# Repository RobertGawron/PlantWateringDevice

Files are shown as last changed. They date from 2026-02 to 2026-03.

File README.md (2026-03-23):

# Plant Watering Device

  

This is a device for watering indoor plants based on the 8-pin PIC10F202-IOT microcontroller.

The goal is to try to make a project on this small MCU and learn how to deal with the limitations of such a small chip, as well as to learn the PIC MCU family ecosystem.

Features:

* **Sensing soil humidity** using a cheap capacitance sensor
* **Display of actual soil humidity and low-level soil humidity when the watering is started;** what is presented on the display is selected by a button, and an additional two LEDs indicate the current reading shown on the display
* Possibility to **change the quantity of water that is dispersed when the soil is detected as dry;** the level can be modified via a button and the current setting is shown on a 10-segment LED bargraph
* Possibility to **select the moisture level when the soil is considered dry** and the watering should be started via a potentiometer

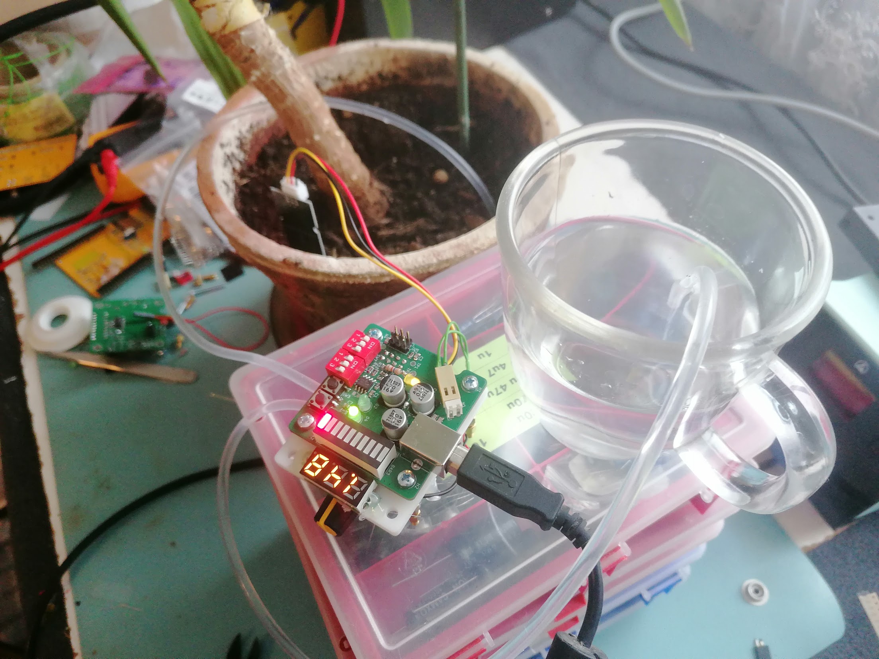
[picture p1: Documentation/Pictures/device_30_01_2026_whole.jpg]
Device in use


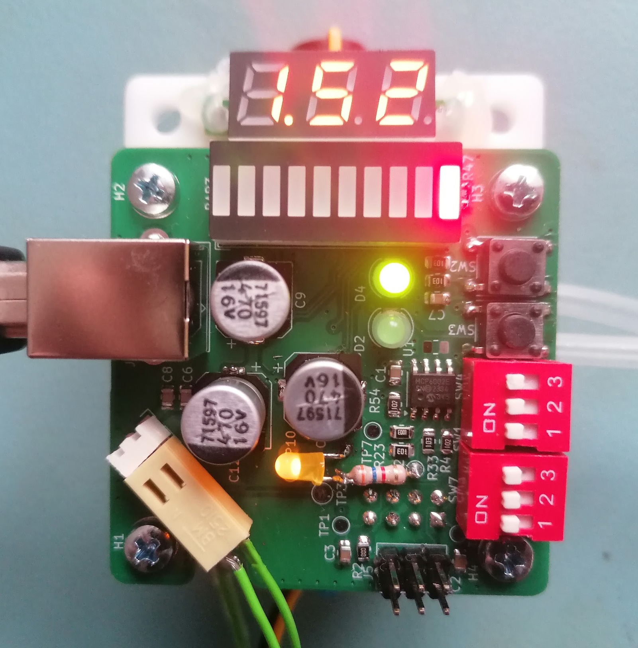
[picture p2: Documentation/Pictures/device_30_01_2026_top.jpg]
Device top


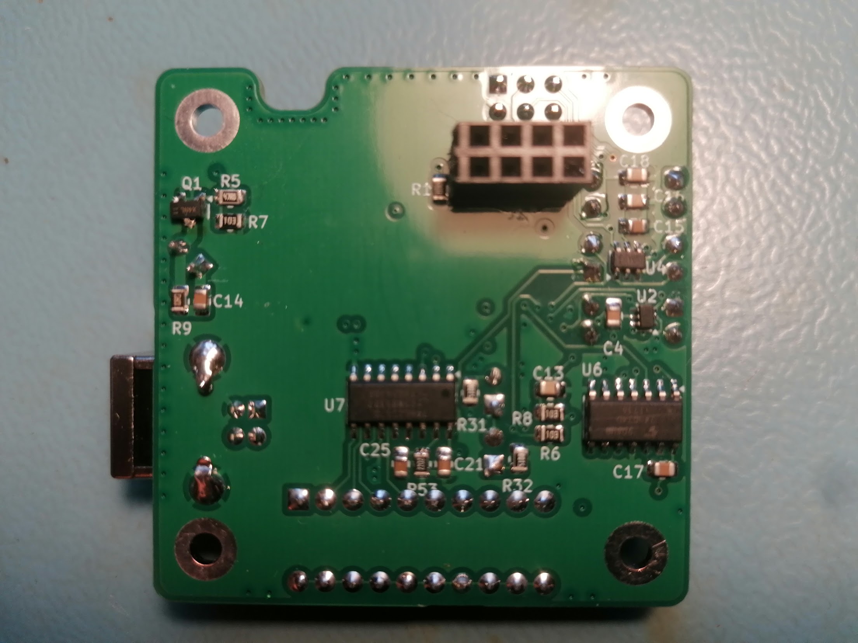
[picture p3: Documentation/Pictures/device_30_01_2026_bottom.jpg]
Device bottom


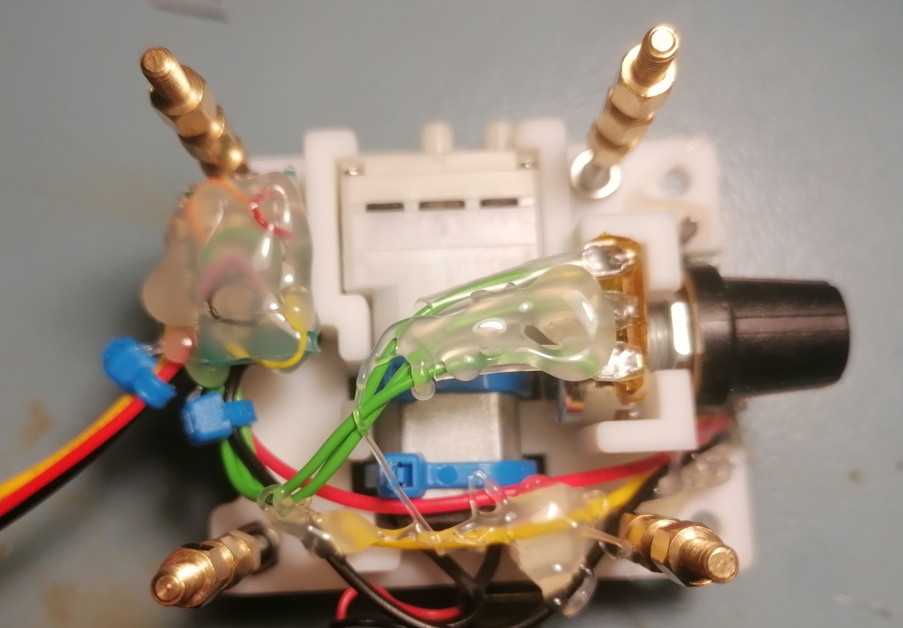
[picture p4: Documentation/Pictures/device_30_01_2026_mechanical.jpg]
Device mechanical


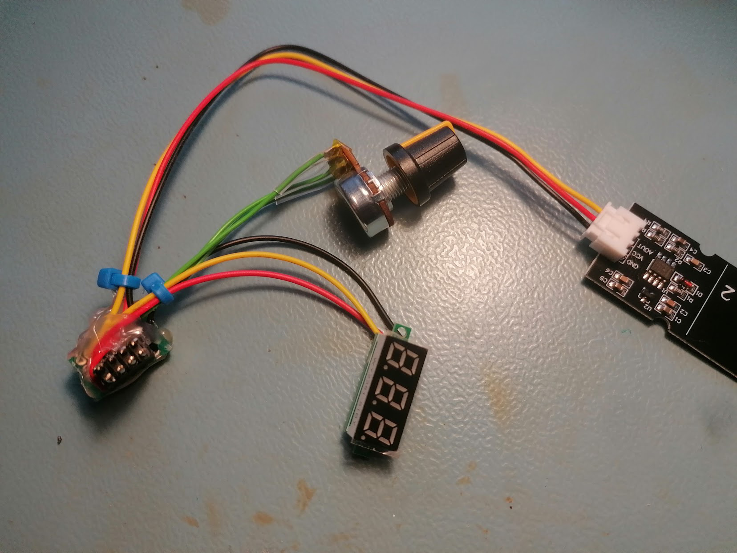
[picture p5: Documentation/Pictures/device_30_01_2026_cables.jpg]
Device cables


## Software

The software is written in C (C99 with _Static_assert from C11).

[Software details.](./Software/README.md)

## Formal Verification

The watering logic is formally verified using frama-c to mathematically prove correctness properties such as:

* Watering is **never activated** when soil moisture is above the threshold
* Watering **always stops** after the configured duration
* No integer overflows or out-of-bounds array accesses occur

This provides stronger guarantees than testing alone — instead of checking specific inputs, it exhaustively verifies **all possible** input combinations.

## Simulation

The software can be run in a web browser to speed up development (no need to flash the device, soil humidity can be simulated as wanted, etc.).

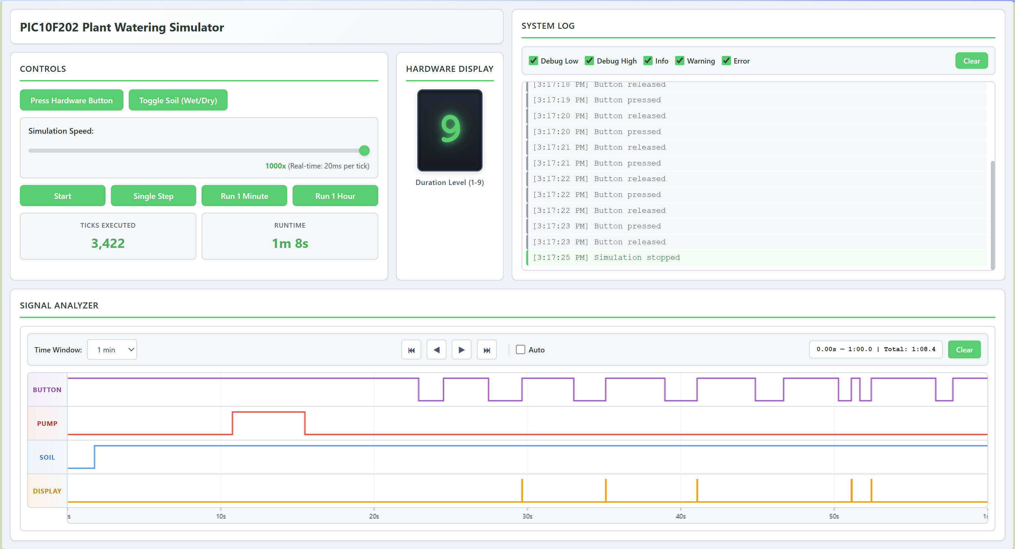
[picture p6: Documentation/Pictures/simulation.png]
Simulation window.


[Simulation details.](./Simulation/README.md)

## Hardware

[Hardware details.](./Hardware/README.md)

Design tools: KiCad

## Mechanical

In order to keep the pump, PCB, display, and potentiometer in one place, a simple 3D printed holder was made.

[Mechanical specifications and assembly details.](./Mechanic/README.md)

Design tools: OpenSCAD and FreeCad

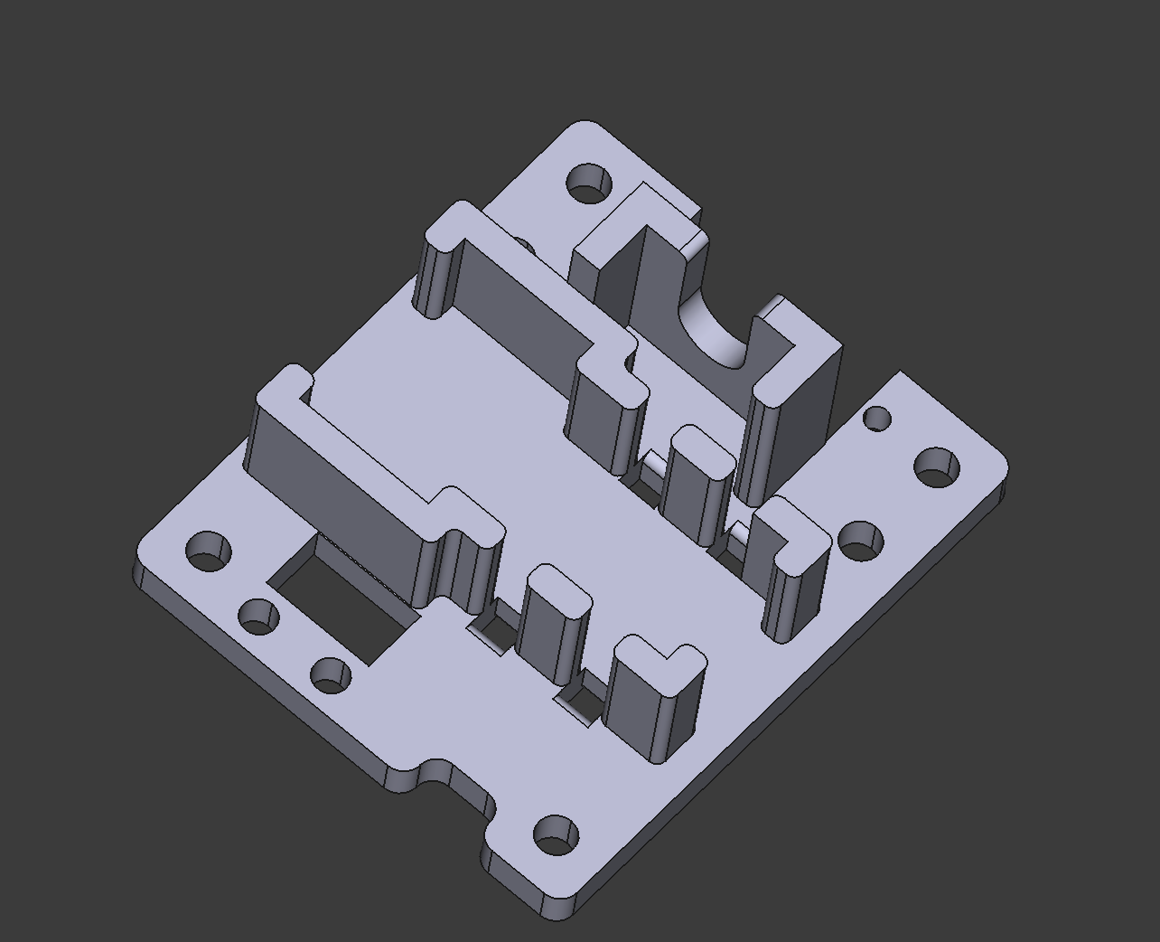
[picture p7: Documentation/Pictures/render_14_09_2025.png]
Mechanical render


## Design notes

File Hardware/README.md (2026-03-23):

# Purpose

This section describes the electronic circuit of this device.

# Tools

The circuit was made in KiCad.

# Used modules

These cheap modules were used in this device; they or their clones are available on AliExpress or similar sites:
* 0.28 Inch LED Digital Display DC Voltmeter 0-100V 2.5-30V
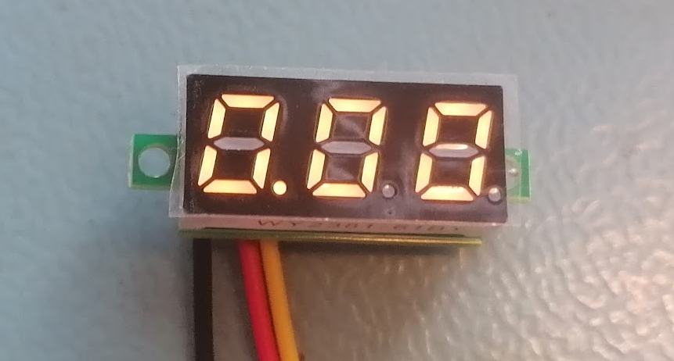
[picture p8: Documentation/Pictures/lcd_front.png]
LCD front

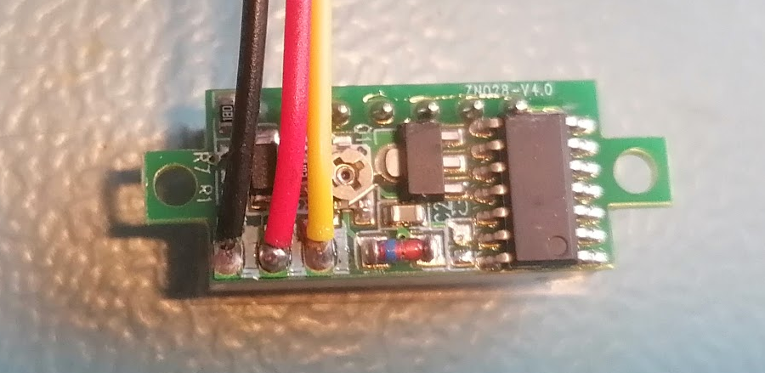
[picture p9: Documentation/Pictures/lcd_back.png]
LCD back

* [JSB1523006 (probably JSB1523008 can be also used): datasheet](https://en.symtek.com.tw/wp-content/uploads/sites/2/2019/03/JSB1523008.pdf
) DC 5V 6V 030 Mini Vacuum Pump Air Pump Oxygen Pump Diaphragm Pump Current 80mA 60KPa 0.6L/min
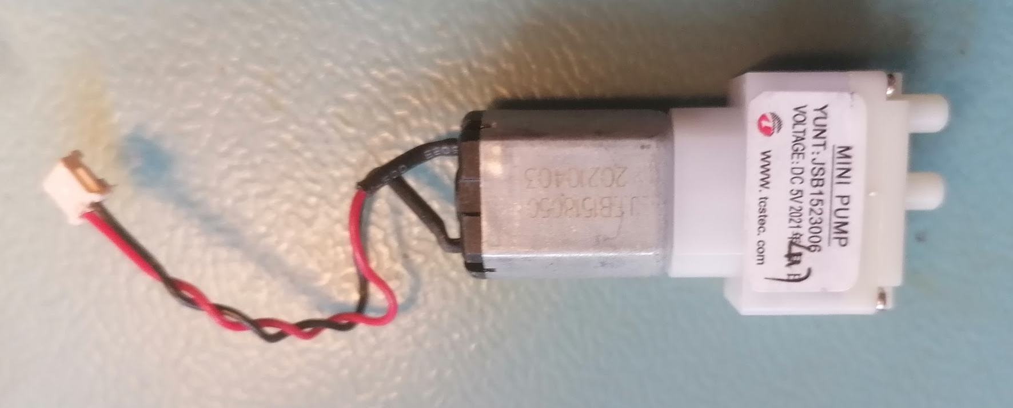
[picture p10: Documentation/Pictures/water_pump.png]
Pump

* Capacitive Soil Moisture Sensor Module Corrosion Resistant Wide Voltage Wire Analog Capacitive Soil Moisture Sensor V1.2
Sensor

* [Potentiometer: datasheet](https://www.tme.eu/Document/44aa78351c5c809af1765772b5b113b7/R16148-1A-1.pdf)
* 4x M2 screw
* 4x M2 nut
* 4x M3 screw
* 4x M3 nut

# Electronic diagrams

Electronic Design DataHandling
Electronic Design DataHandling
Electronic Design Display
Electronic Design HumiditySensor
Electronic Design PowerManagement

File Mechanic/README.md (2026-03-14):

# Purpose

This is a 3D model of a chassis designed to hold:
* the water pump
* main PCB

# Tools

The model was made in OpenSCAD version 2021.01 and then exported to FreeCAD version 1.0.

# Usage

* Model the chassis in OpenScad
* Open FreeCad, create new body, File -> Import, select Main.scad
* Add fillets
* Export for 3d printing

# Datasheets

[Datasheets](../Hardware/README.md)

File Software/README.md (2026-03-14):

# Purpose
[PIC10F202-IOT](http://ww1.microchip.com/downloads/en/DeviceDoc/41239D.pdf
) chip is a small PIC family microcontroller used for gathering soil humidity level and driving the water pump. This section describes project structure, setup, and flashing the device.

# Architecture

Activity Diagram

# Prerequisites

## Hardware:
* I use PICKit3 to program the chip.
  * The pro is that it's cheap and does the job.
  * The con is that it's marked as obsolete by Microchip; I've found it hard/impossible to integrate with the MPLAB ecosystem.

## Software

* [Install MPLAB X IDE](https://www.microchip.com/en-us/tools-resources/develop/mplab-x-ide), use the latest version
* If you (like me) don't see PICKit3 enumerated in MPLAB IPE, switch to flashing using open source [PICkit tool](https://github.com/jaka-fi/PICkitminus)
* Visual Studio Code - more modern/lightweight than developing in MPLAB X IDE.
* [Assembly highlighting](https://marketplace.visualstudio.com/items?itemName=zhihao1021.pic18-assembly-language) - it's not the most suited for this assembly dialect but I didn't find anything better.

# Usage

* In VS Code open folder Software/PlantWateringDevice.X
* You will be asked if you want to import the project. Do it.
* Press Ctrl+Shift+B to build. The file to be flashed is (from project root perspective) in ```Software/PlantWateringDevice.X/dist/default/production/PlantWateringDevice.X.production.hex```
* Use PICkit (mentioned in requirements) or MPLAB IPE to flash it.

**Note:** the VS Code configuration is for Windows and assumes you are using ```MPLAB v6.30```. If that's not the case, update the paths in [PlantWateringDevice.X/.vscode/tasks.json](./PlantWateringDevice.X/.vscode/tasks.json)

# Formal Verification

Fragma-C is used, [more details here](../DevOps/README.md).

# Unit Tests

There is a small set of manual integration tests, [more details here](../DevOps/README.md).

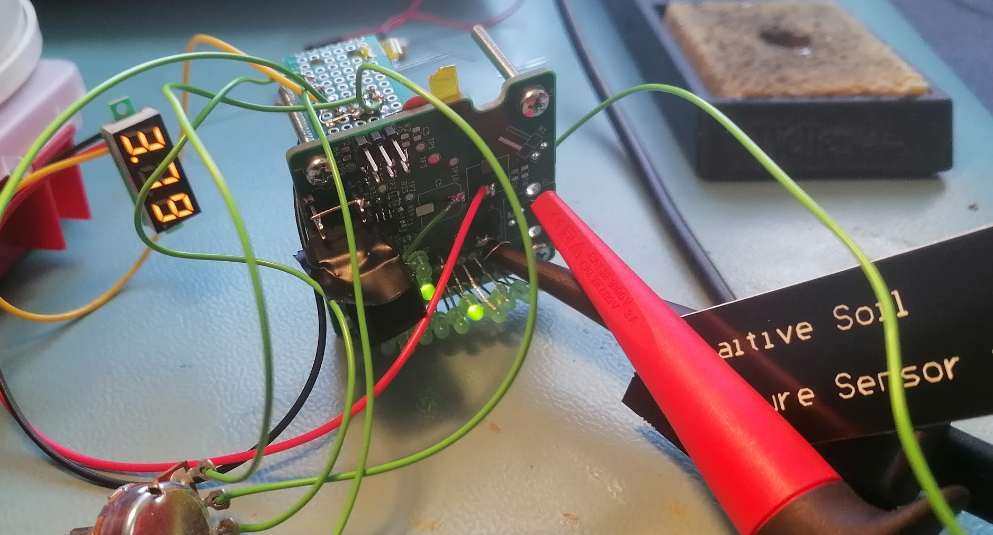
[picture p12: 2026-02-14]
Documentation/Pictures/device_27_01_2026.png

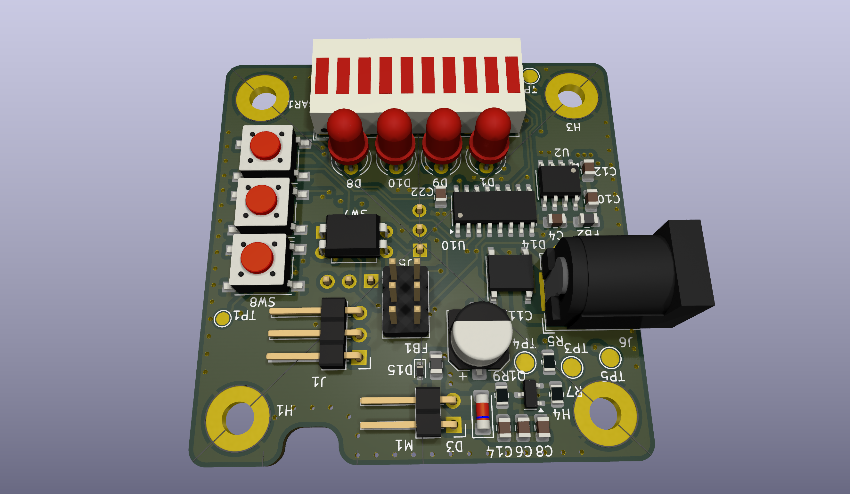
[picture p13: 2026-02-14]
Documentation/Pictures/render_06_09_2025.png

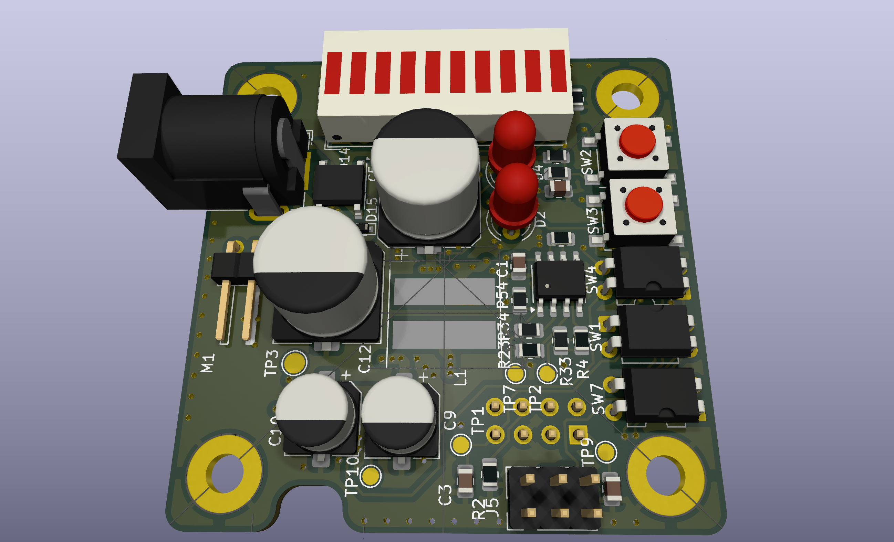
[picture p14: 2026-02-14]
Documentation/Pictures/render_07_09_2025.png

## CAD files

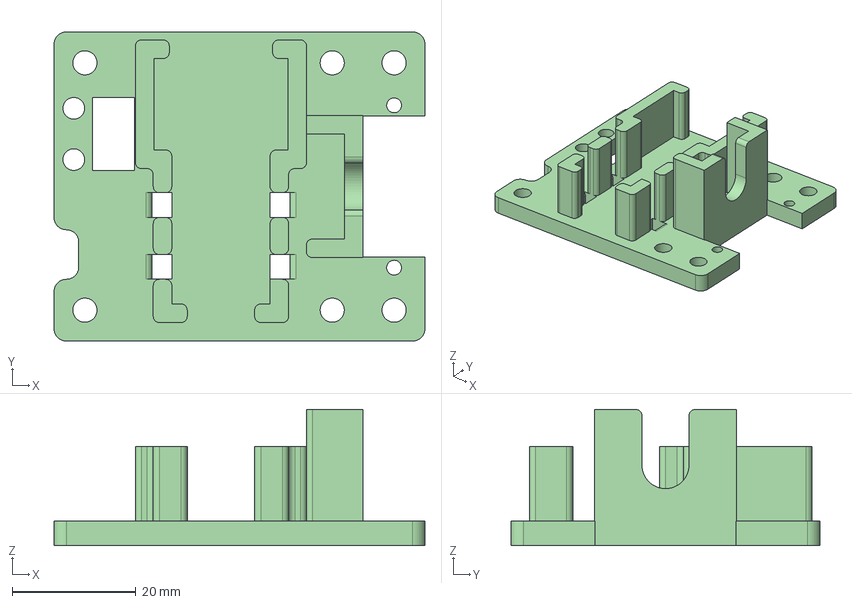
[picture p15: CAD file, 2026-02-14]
Mechanic/FreeCAD/BottomHolder.FCStd
60.0 x 50.0 x 22.0 mm
circle
circle001
circle002
circle003
circle004
circle005
circle006
circle007
circle008
circle009
circle010

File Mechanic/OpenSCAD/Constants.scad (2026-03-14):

// ================= General =================================
smoothness = 50;        // Circle resolution
manufacturer_tolerance = 0.4; // Tolerance of 3D prints from printing factory

// =============== PCB related dimensions ====================

// top view
pcb_size_x = 48;           
pcb_size_y = 45;

// Hole for mounting screws that hold PCB
hole_diameter = 2.5;  

// ===================== MainBoard =========================== 
mainboard_z = 3;

// ================== Pump Holder =============================
// Pump holder constants used for holder and for holes for zipties
// todo move it somewhere

motor_w = 15.3 + 0.2 + manufacturer_tolerance;

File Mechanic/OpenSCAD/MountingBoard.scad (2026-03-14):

include <Constants.scad>

hole_distance = 3.5;       // from hole center to PCB edge

// PCB base shape (2D)
module pcb_base() 
{
    square([pcb_size_x, pcb_size_y], center = true);
}

// Single mounting hole (2D)
module mounting_hole_2d(x, y, hole_diameter) 
{
    translate([x, y, 0])
    {
        circle(d = hole_diameter);
    }
}

// All mounting holes (2D)
module mounting_holes_2d(hole_diameter) 
{
    // Calculate the absolute X and Y positions once
    dx = (pcb_size_x / 2) - hole_distance;
    dy = (pcb_size_y / 2) - hole_distance;

    // Loop through multipliers -1 (left/bottom) and 1 (right/top)
    for (x_mult = [-1, 1]) 
    {
        for (y_mult = [-1, 1]) 
        {
            x = x_mult * dx;
            y = y_mult * dy;

            mounting_hole_2d(x, y, hole_diameter);
        }
    }
}

module connector_slot_2d() 
{
    // bottom left pcb corner is the reference point
    x = -(pcb_size_x / 2);
    y  = -(pcb_size_y / 2);

    // taken from dimensions measurement on kicad pcb
    x_offset = 6.5;
    y_offset = 0;

    dx = pcb_size_x - (2 * x_offset);
    dy = 11.65;
    
    translate([x + x_offset, y + y_offset, 0])
    { 
        square([dx, dy]);
    }
}

// Main 2D mounting board
module mounting_board_2d() 
{
    difference() 
    {
        pcb_base();
        connector_slot_2d();
    }
}

// 3D extruded version
module mounting_board_3d() 
{
    linear_extrude(height = mainboard_z) 
    {
        mounting_board_2d();
    }
}

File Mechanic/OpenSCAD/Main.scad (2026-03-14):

include <MountingBoard.scad>
include <PumpHolder.scad>
//include <Potentiometer.scad>
include <ZipTieBracket.scad>

$fn = smoothness;

// The pump doesn't need to be exactly at the center; it was slightly moved
// to give space for socket connector. This offset is important for pump
// holder and zip ties
pump_x_offset = 0;
pump_y_offset = 3;

module bottom_legs_3d() {
    // should slightly higher than pump holder to avoid that
    // the pump would touch surface on which the device stands.
    support_legs_height = mainboard_z 
                            + pump_thickness_z + 1.5;

    // should be bigger than the screw that goes into it.
    support_legs_diameter = 6;
    
    linear_extrude(height = support_legs_height)
    {
        mounting_holes_2d(support_legs_diameter);
    }
}

module top_legs_3d() {
    // this should be enough space, limiting factor are 
    // tantal caps and usb connector on the PCB. 
    // Note that there is a cutout for bottom sockets so
    // theirs height is not important here.
    top_support_legs_height = 4;

    // Should be bigger than the screw that goes into it.
    // Unlike bottom legs here we are limited b PCB components
    // clearance, if it will be to big, it will collide with
    // nearby PCB components.
    support_legs_diameter = 6;
    
    translate([0, 0, -top_support_legs_height]) 
    {
        linear_extrude(height = top_support_legs_height)
        {
            mounting_holes_2d(support_legs_diameter);
        }
    }
}

// bras inserts to mount the pcb
module top_legs_inserts_3d() {
    // this should be enough space, limiting factor are 
    // tantal caps and usb connector on the PCB. 
    // Note that there is a cutout for bottom sockets so
    // theirs height is not important here.
    support_legs_height = 7;

    // Should be bigger than the screw that goes into it.
    // Unlike bottom legs here we are limited b PCB components
    // clearance, if it will be to big, it will collide with
    // nearby PCB components.
    support_legs_diameter = 3.2;
    
    translate([0, 0, -support_legs_height]) 
    {
        linear_extrude(height = support_legs_height)
        {
            mounting_holes_2d(support_legs_diameter);
        }
    }
}

module zipties_3d()
{
        rotate ([0,0,90]) { 
            ziptie_height = mainboard_z 
                                + 2*pump_thickness_z;
        
            linear_extrude(height = ziptie_height) 
            {
                x = pump_y_offset;
                y = pcb_size_y/2 + pump_x_offset;
                z = -mainboard_z;
                
                translate([x, y, z]) 
                {
                    zipties_2d();
                }
            }
        }
    }

module model_without_zipties_3d() {
    union() {
        mounting_board_3d();
        bottom_legs_3d();
        top_legs_3d();
        
        // design with directions from first version
        // I will just rotate it instead of recreating it properly
        rotate ([0,0,90])
        {
            translate([ pump_y_offset, 
                        -pcb_size_y/2 + pump_x_offset, 
                        mainboard_z]) 
            {
                pump_rails_3d();
            }
        }
    }
}

module whole_model_3d() {

    difference() 
    {

    difference() 
    {
        // the lose so far
        model_without_zipties_3d();

        // remove material for zip ties
        zipties_3d();
        }

         top_legs_inserts_3d();
            }
}

whole_model_3d();

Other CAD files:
Mechanic/OpenSCAD/PumpHolder.scad
Mechanic/OpenSCAD/ZipTieBracket.scad

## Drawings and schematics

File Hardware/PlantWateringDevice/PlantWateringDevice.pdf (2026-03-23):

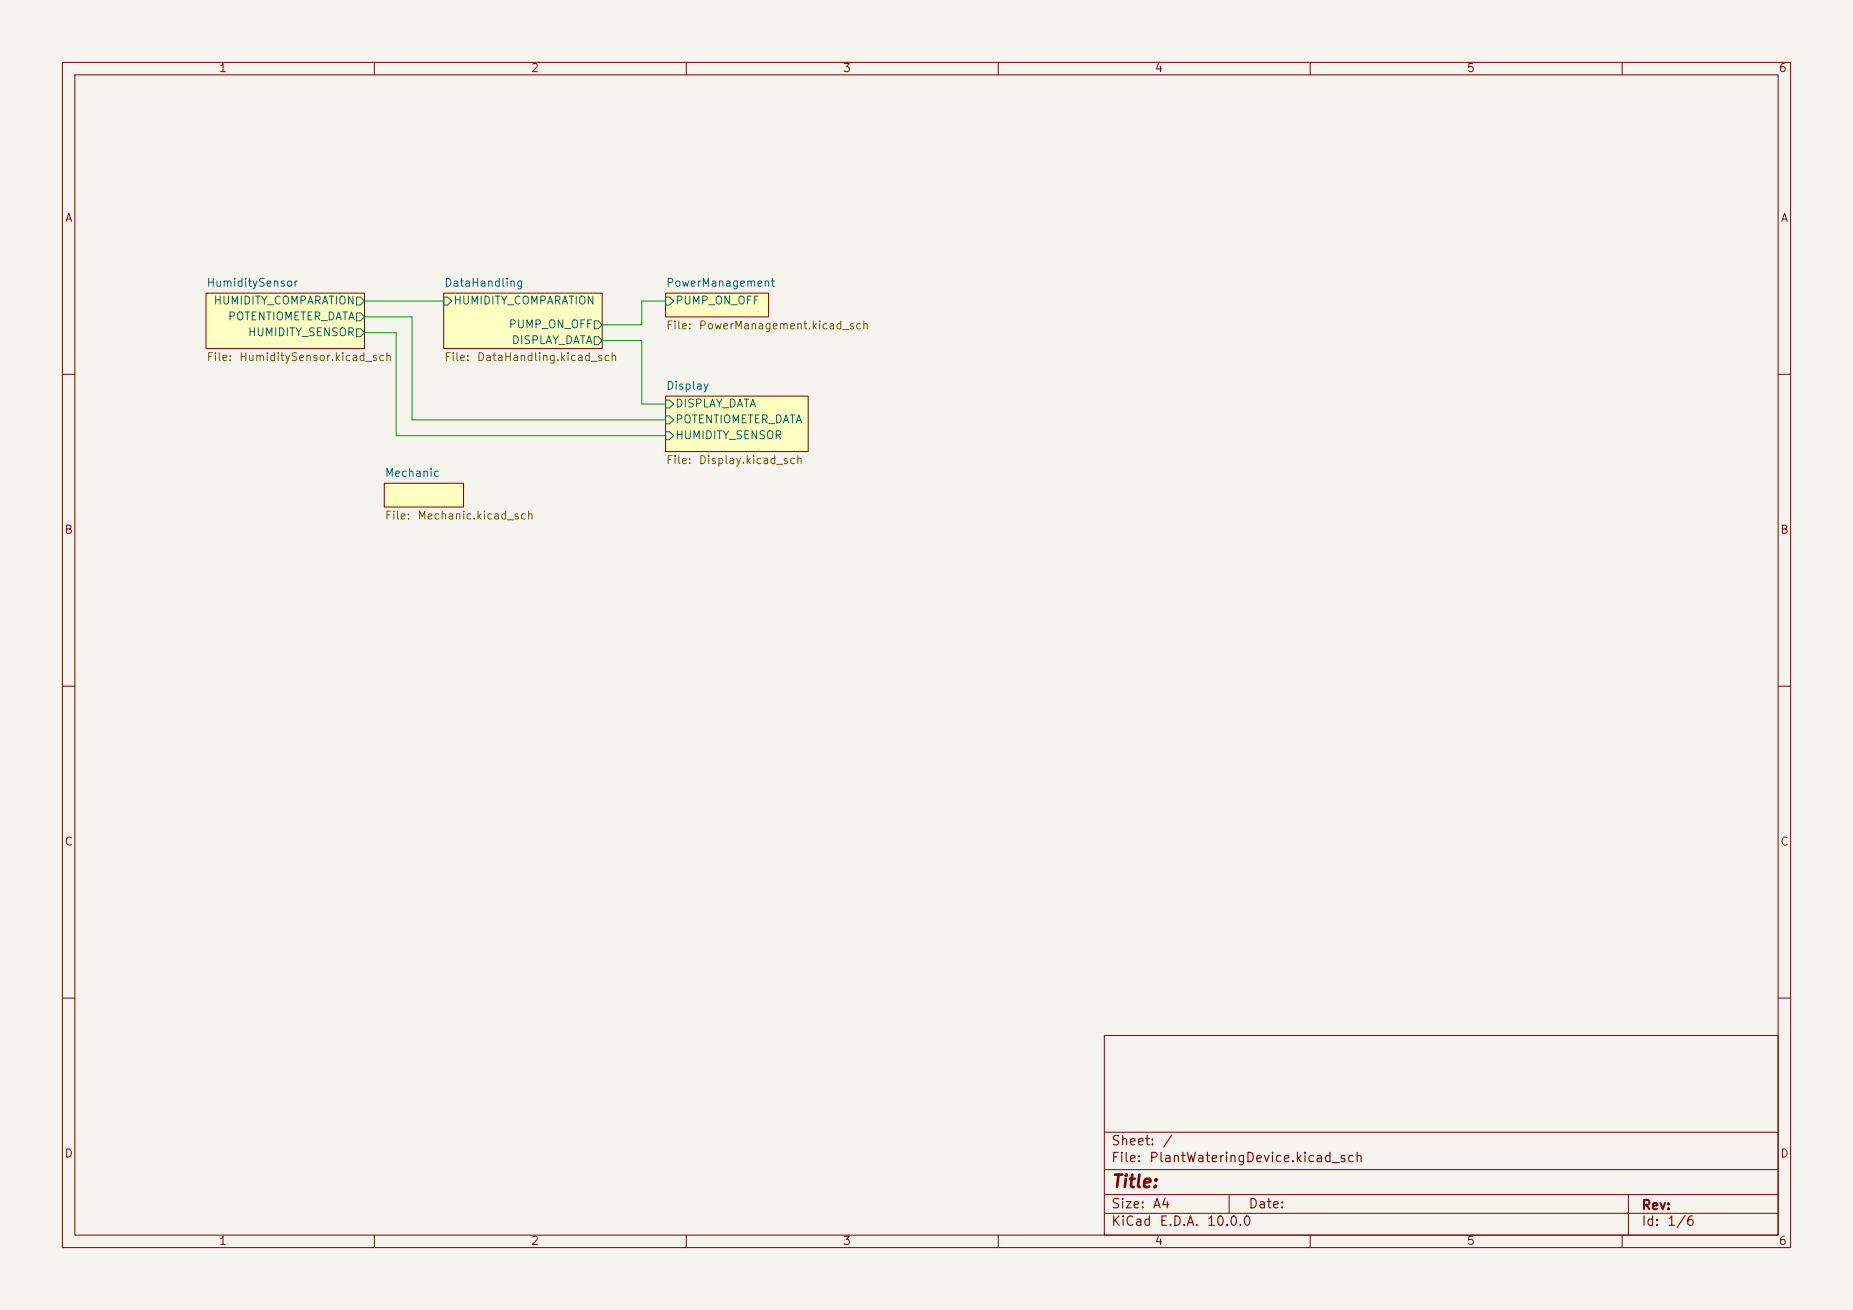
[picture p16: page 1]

Size: A4 | Rev:
KiCad E.D.A. 10.0.0 | Id: 1/6

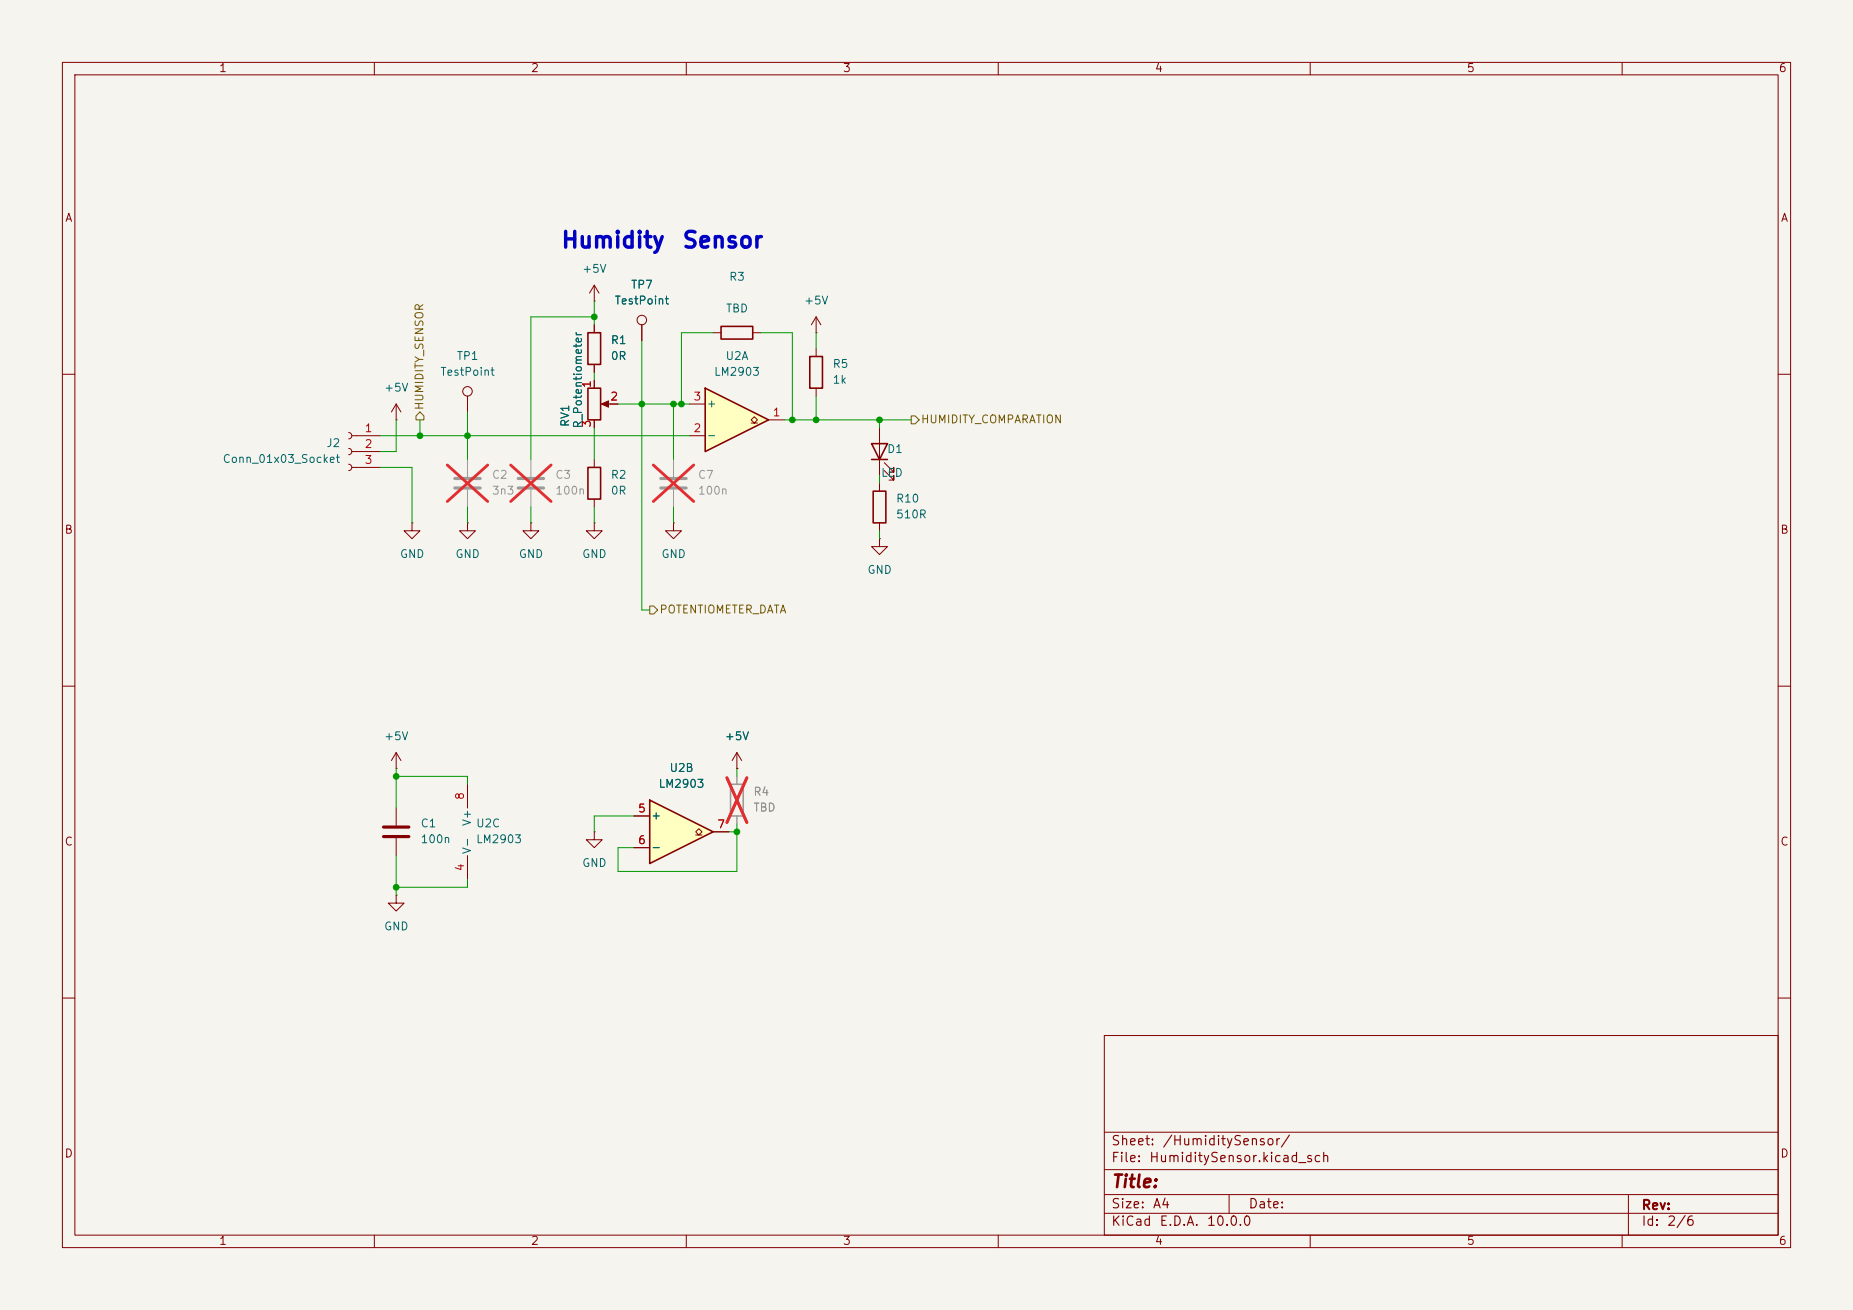
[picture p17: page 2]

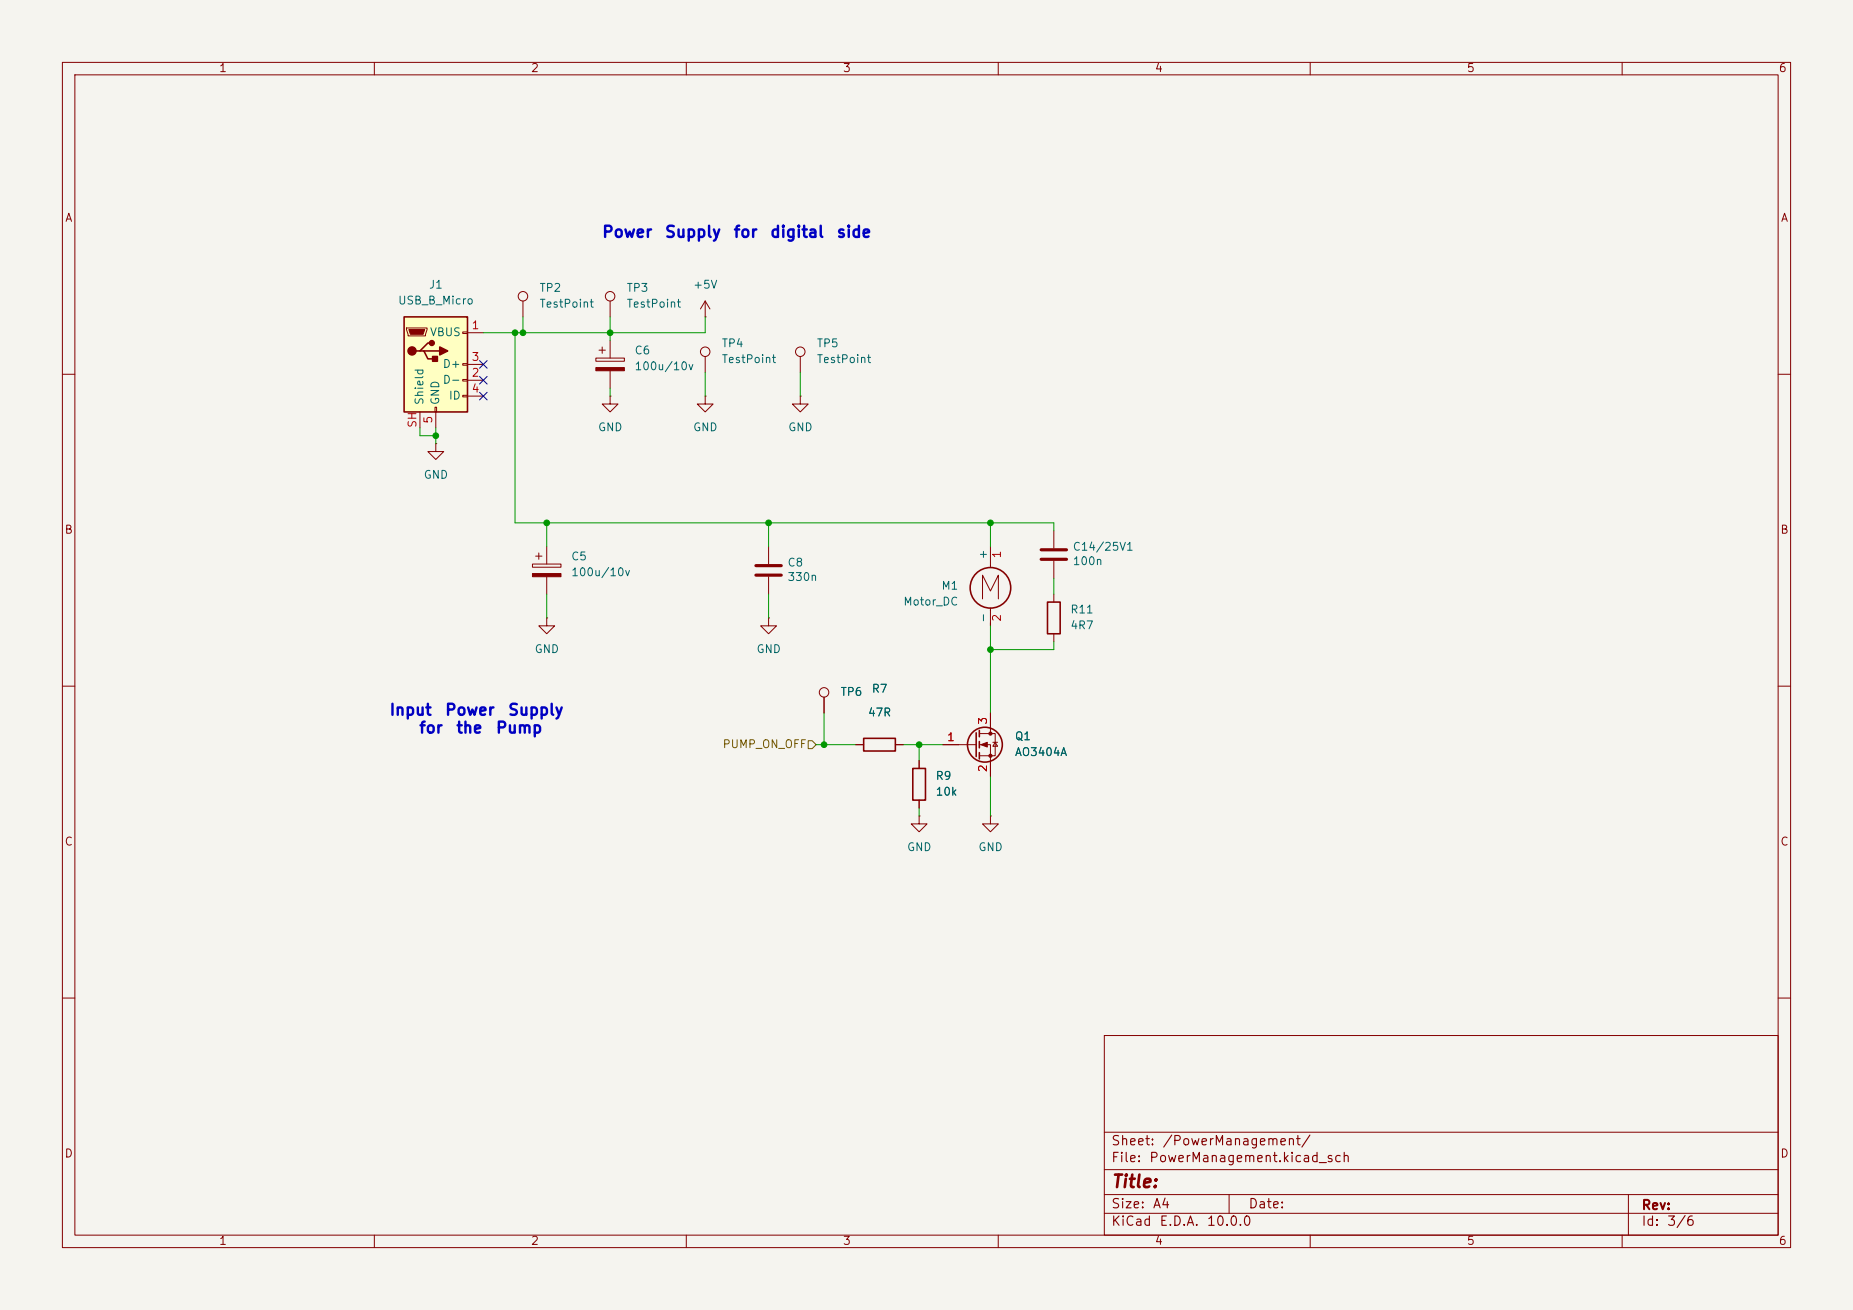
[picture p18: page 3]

TestPoint +5V PUMP_ON_OFF Power Supply for digital side
TestPoint C5

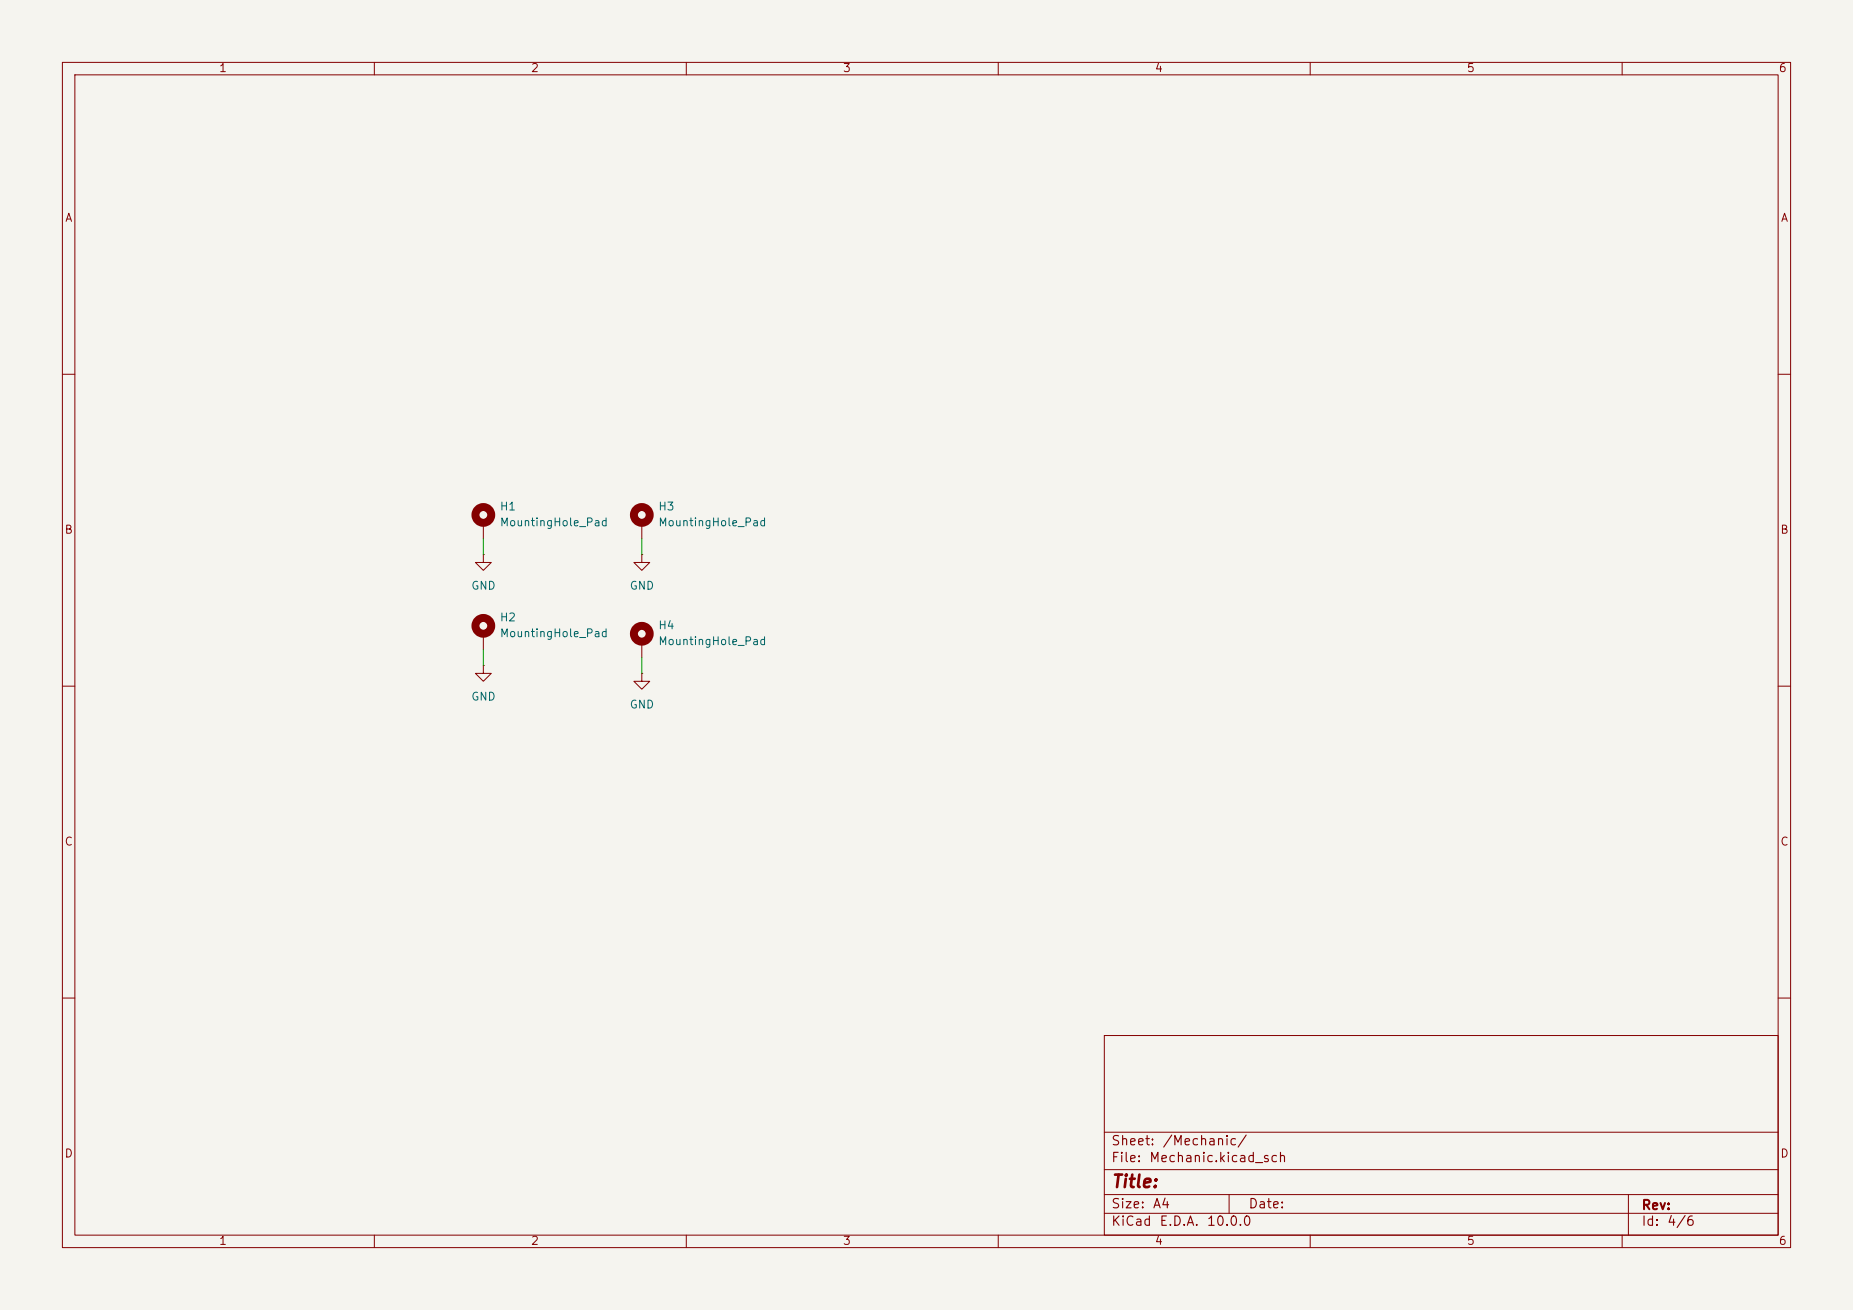
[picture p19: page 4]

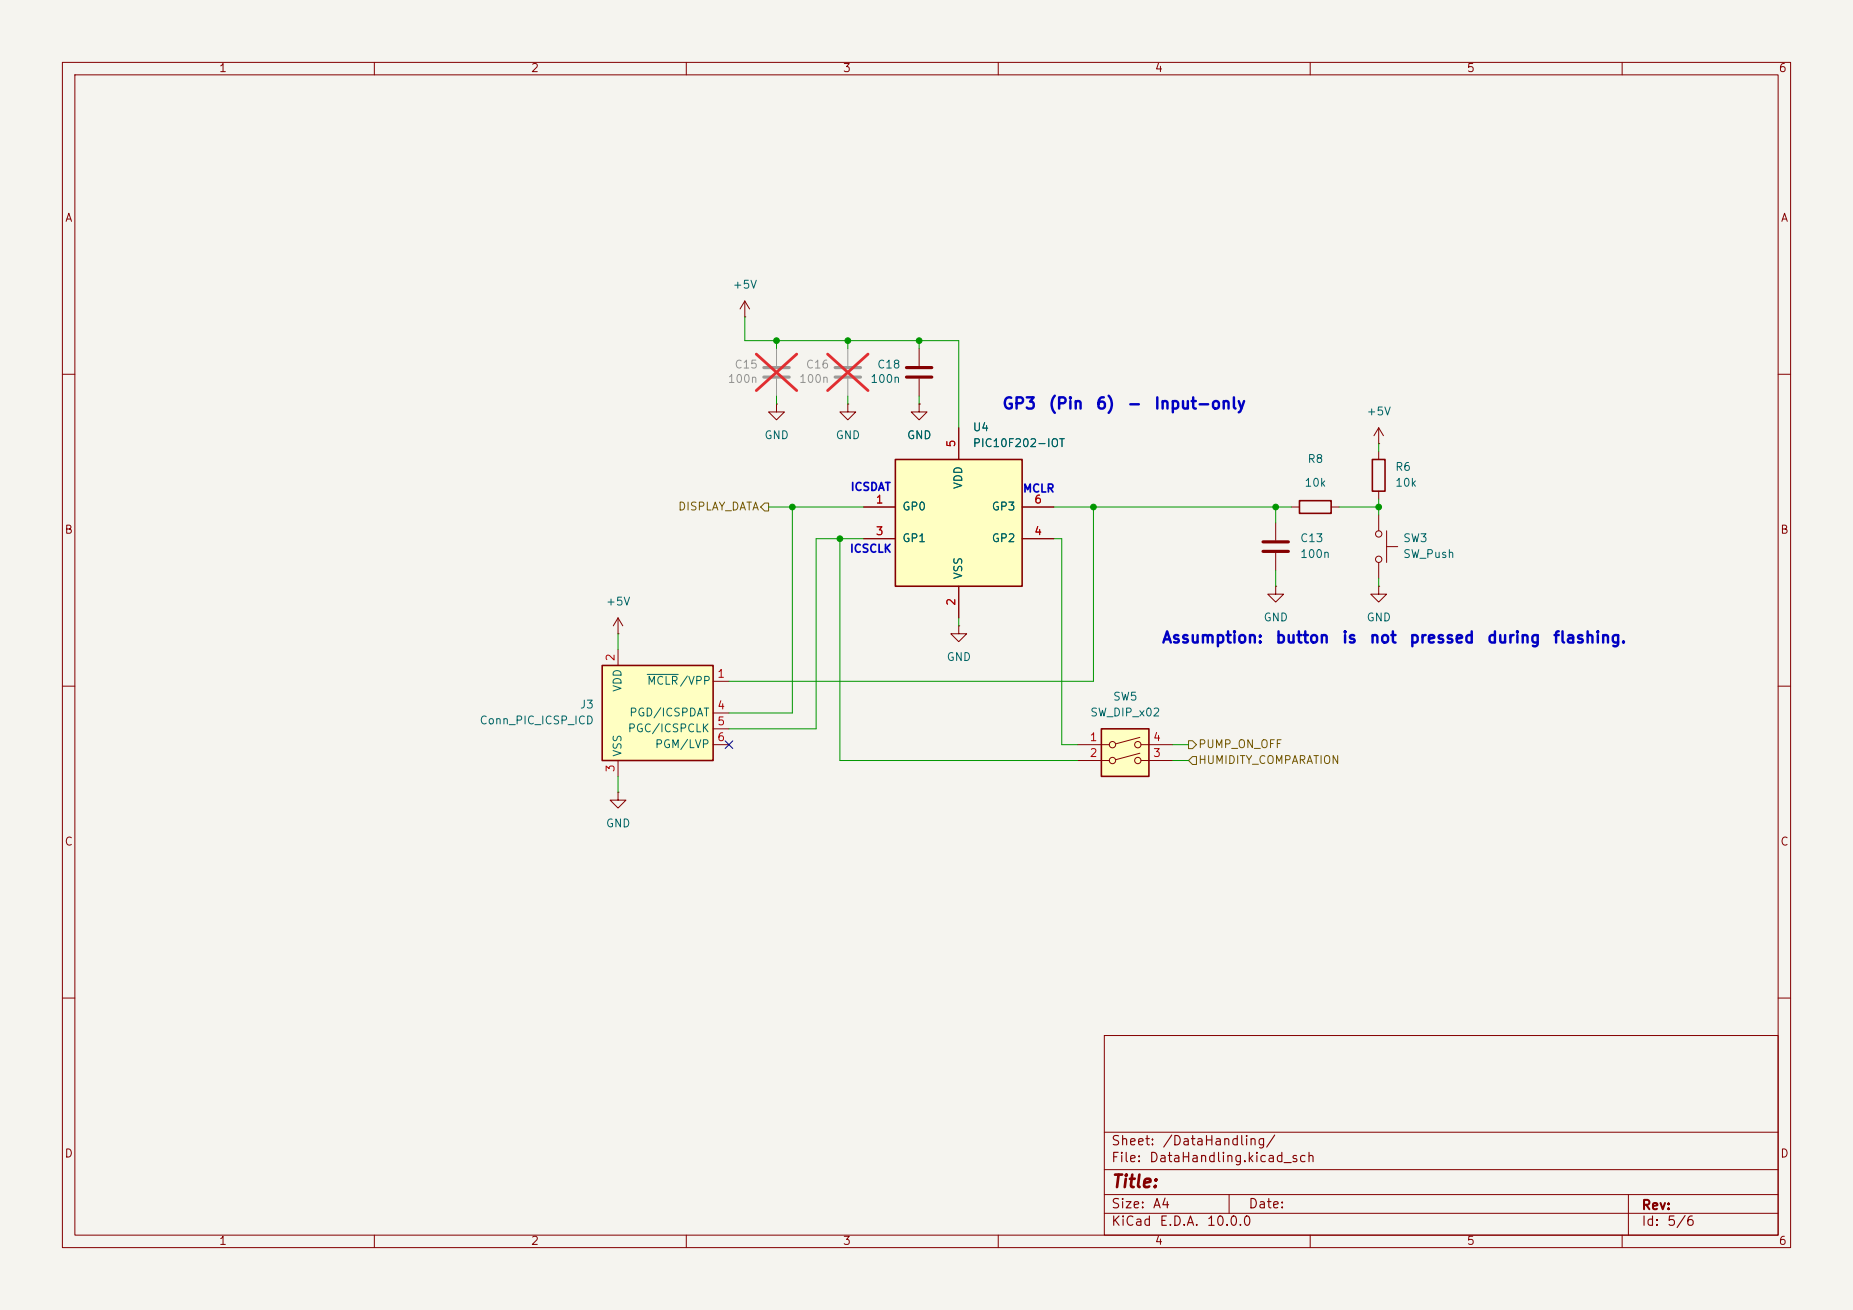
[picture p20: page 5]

3 PGD/ICSPDAT 4 PGC/ICSPCLK 5 PGM/LVP 6

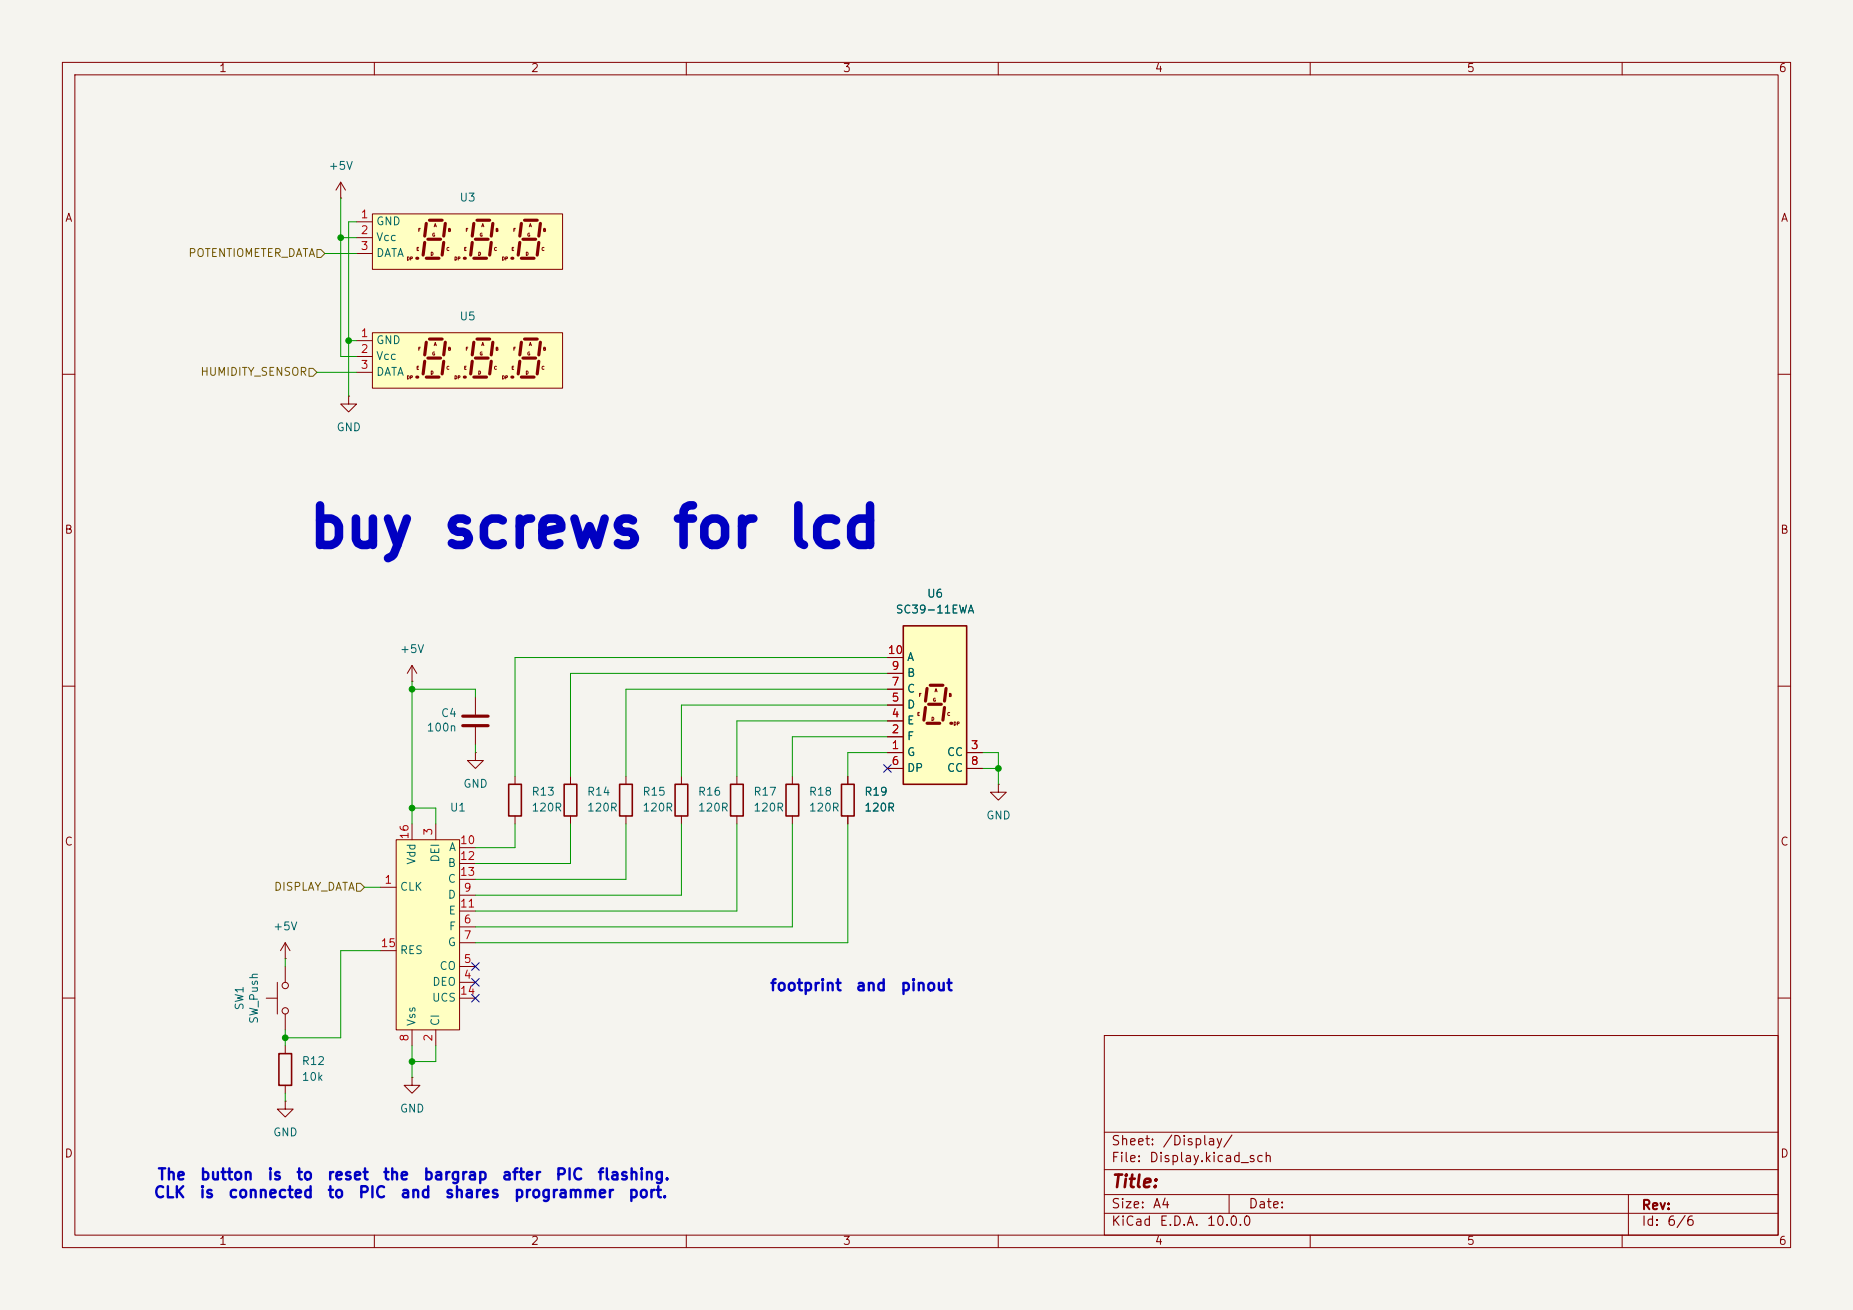
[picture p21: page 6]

The button is to reset the bargrap after PIC flashing.
CLK is connected to PIC and shares programmer port.

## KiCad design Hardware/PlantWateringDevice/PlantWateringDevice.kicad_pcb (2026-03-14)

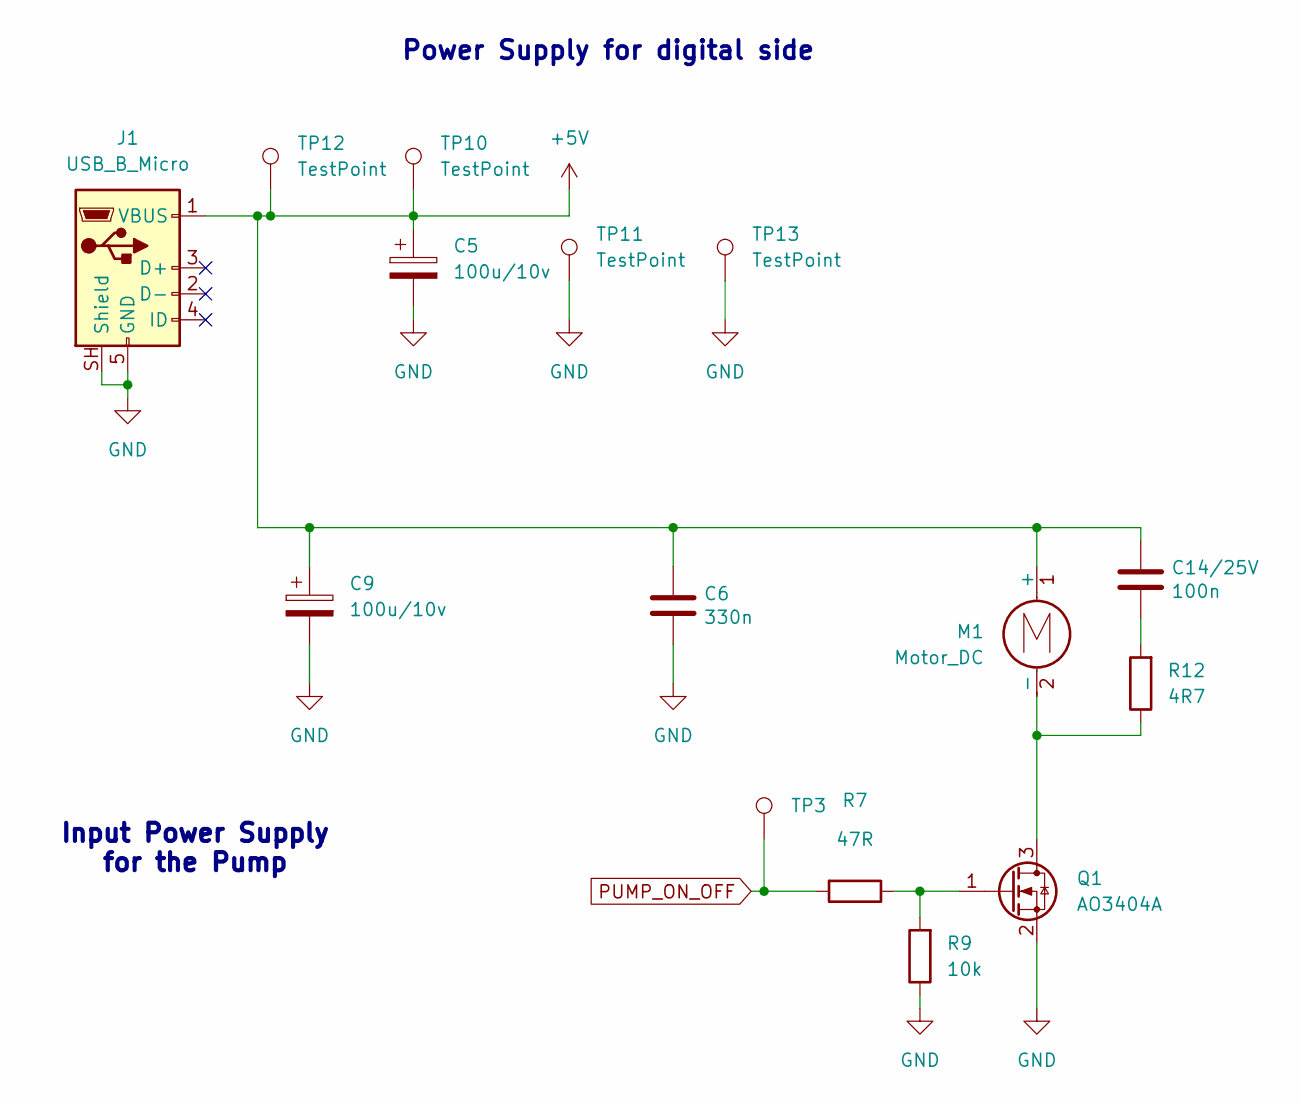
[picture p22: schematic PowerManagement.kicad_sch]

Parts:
C5, C9: 100u/10v; CP_EIA-6032-28_Kemet-C
C6: 330n; C_0603_1608Metric
C14/25V: 100n; C_0603_1608Metric
J1: USB_B_Micro; USB_Micro-B_Molex-105017-0001_Extra_Mechanical_Pads
M1: Motor_DC; JST_EH_B2B-EH-A_1x02_P2.50mm_Vertical
Q1: AO3404A; SOT-23
R7: 47R; R_0603_1608Metric
R9: 10k; R_0603_1608Metric
R12: 4R7; R_0603_1608Metric
TP3, TP10, TP11, TP12, TP13: TestPoint; TestPoint_Pad_D1.5mm

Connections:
+5V: C5.1, C6.1, C9.1, C14/25V.1, J1.1 (VBUS), M1.1 (+), TP10.1 (1_1), TP12.1 (1_1); also elsewhere on the board
GND: C5.2, C6.2, C9.2, J1.5 (GND), J1.SH (Shield), Q1.2 (S), R9.1, TP11.1 (1_1), TP13.1 (1_1); also elsewhere on the board
unnamed 5: C14/25V.2, R12.2; also elsewhere on the board
unnamed: M1.2 (-), Q1.3 (D), R12.1
unnamed: Q1.1 (G), R7.1, R9.2
PUMP_ON_OFF: R7.2, TP3.1 (1_1); also elsewhere on the board

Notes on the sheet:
Power Supply for digital side
Input Power Supply for the Pump

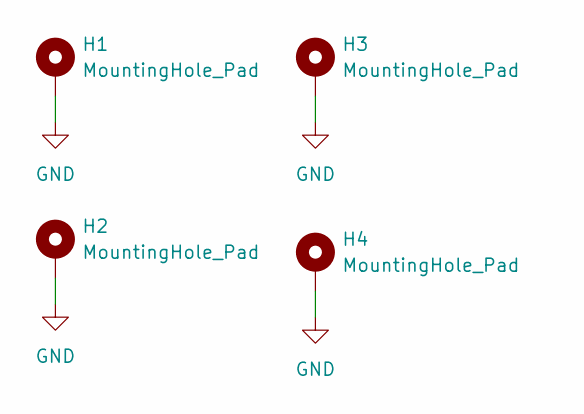
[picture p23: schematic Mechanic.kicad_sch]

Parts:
H1, H2, H3, H4: MountingHole_Pad; MountingHole_2.5mm_Pad

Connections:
GND: H1.1 (1_1), H2.1 (1_1), H3.1 (1_1), H4.1 (1_1); also elsewhere on the board

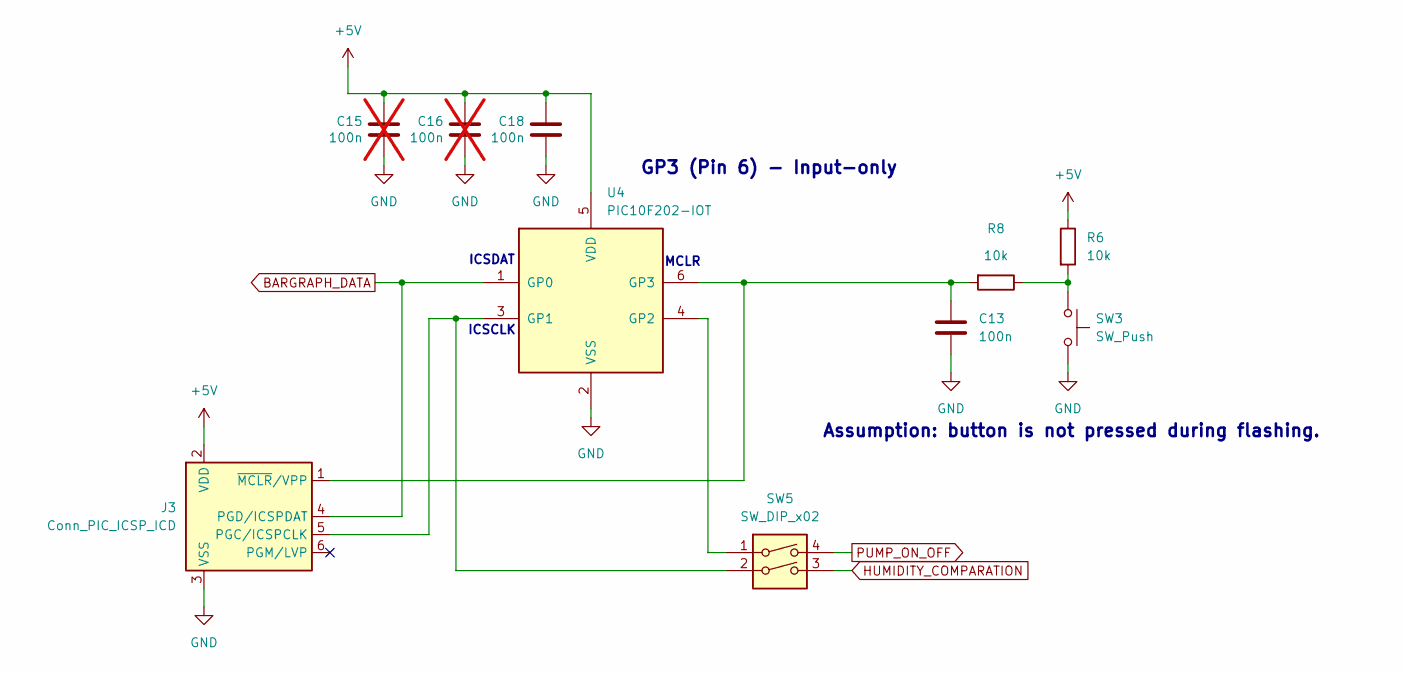
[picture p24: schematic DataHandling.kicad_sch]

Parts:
C13, C18: 100n; C_0603_1608Metric
C15, C16: 100n; C_0603_1608Metric; not fitted
J3: Conn_PIC_ICSP_ICD; PinHeader_1x06_P2.54mm_Vertical
R6, R8: 10k; R_0603_1608Metric
SW3: SW_Push; SW_SPST_PTS645Sx43SMTR92
SW5: SW_DIP_x02; DIP-4_W7.62mm
U4: PIC10F202-IOT; SOT-23-6

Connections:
+5V: C15.1, C16.1, C18.1, J3.2 (VDD), R6.1, U4.5 (VDD); also elsewhere on the board
BARGRAPH_DATA: J3.4 (PGD/ICSPDAT), U4.1 (GP0); also elsewhere on the board
GND: C13.2, C15.2, C16.2, C18.2, J3.3 (VSS), SW3.1, U4.2 (VSS); also elsewhere on the board
HUMIDITY_COMPARATION: SW5.3; also elsewhere on the board
unnamed: J3.5 (PGC/ICSPCLK), SW5.2, U4.3 (GP1)
unnamed: C13.1, J3.1 (~MCLR/VPP), R8.2, U4.6 (GP3)
unnamed: R6.2, R8.1, SW3.2
unnamed: SW5.1, U4.4 (GP2)
PUMP_ON_OFF: SW5.4; also elsewhere on the board

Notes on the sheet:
ICSCLK
GP3 (Pin 6) - Input-only
ICSDAT
Assumption: button is not pressed during flashing.
MCLR

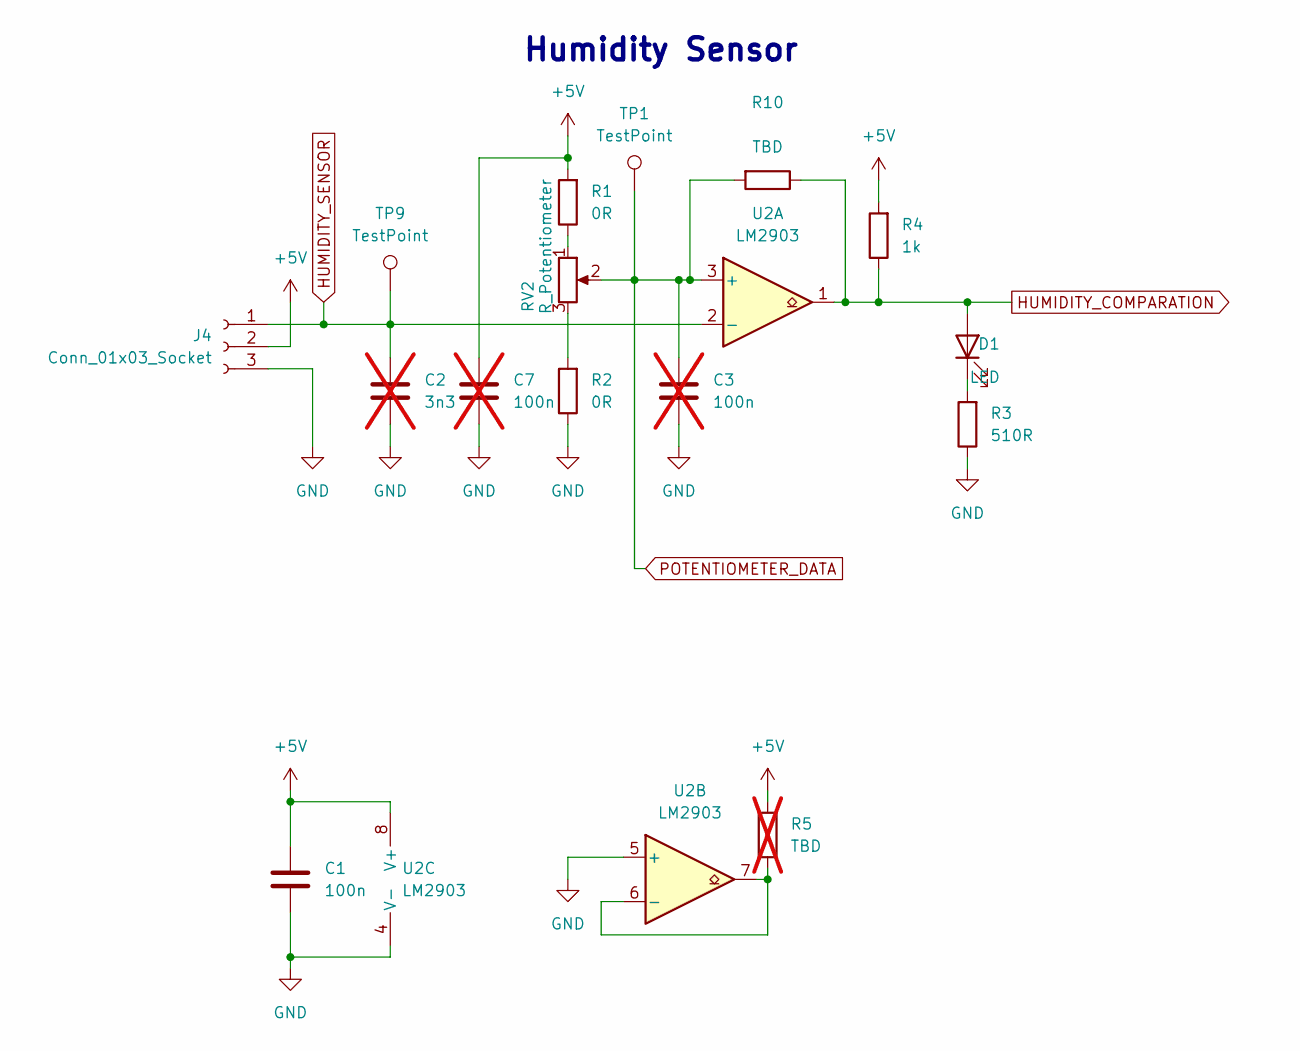
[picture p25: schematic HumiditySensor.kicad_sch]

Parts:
C1: 100n; C_0603_1608Metric
C2: 3n3; C_0603_1608Metric; not fitted
C3, C7: 100n; C_0603_1608Metric; not fitted
D1: LED; LED_D4.0mm
J4: Conn_01x03_Socket; JST_EH_B3B-EH-A_1x03_P2.50mm_Vertical
R1, R2: 0R; R_0603_1608Metric
R3: 510R; R_0603_1608Metric
R4: 1k; R_0603_1608Metric
R5: TBD; R_0603_1608Metric; not fitted
R10: TBD; R_0603_1608Metric
RV2: R_Potentiometer; Potentiometer_Alps_RK09L_Single_Vertical
TP1, TP9: TestPoint; TestPoint_Pad_D1.5mm
U2: LM2903; TSSOP-8_3x3mm_P0.65mm

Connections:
+5V: C1.1, C7.1, J4.2, R1.2, R4.2, R5.2, U2.8 (V+); also elsewhere on the board
GND: C1.2, C2.2, C3.2, C7.2, J4.3, R2.1, R3.1, U2.4 (V-), U2.5 (+); also elsewhere on the board
HUMIDITY_COMPARATION: D1.2 (A), R4.1, R10.1, U2.1; also elsewhere on the board
HUMIDITY_SENSOR: C2.1, J4.1, TP9.1 (1_1), U2.2 (-); also elsewhere on the board
unnamed: D1.1 (K), R3.2
unnamed: R1.1, RV2.1
unnamed: R2.2, RV2.3
unnamed: R5.1, U2.6 (-), U2.7
POTENTIOMETER_DATA: C3.1, R10.2, RV2.2, TP1.1 (1_1), U2.3 (+); also elsewhere on the board

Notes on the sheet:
Humidity Sensor

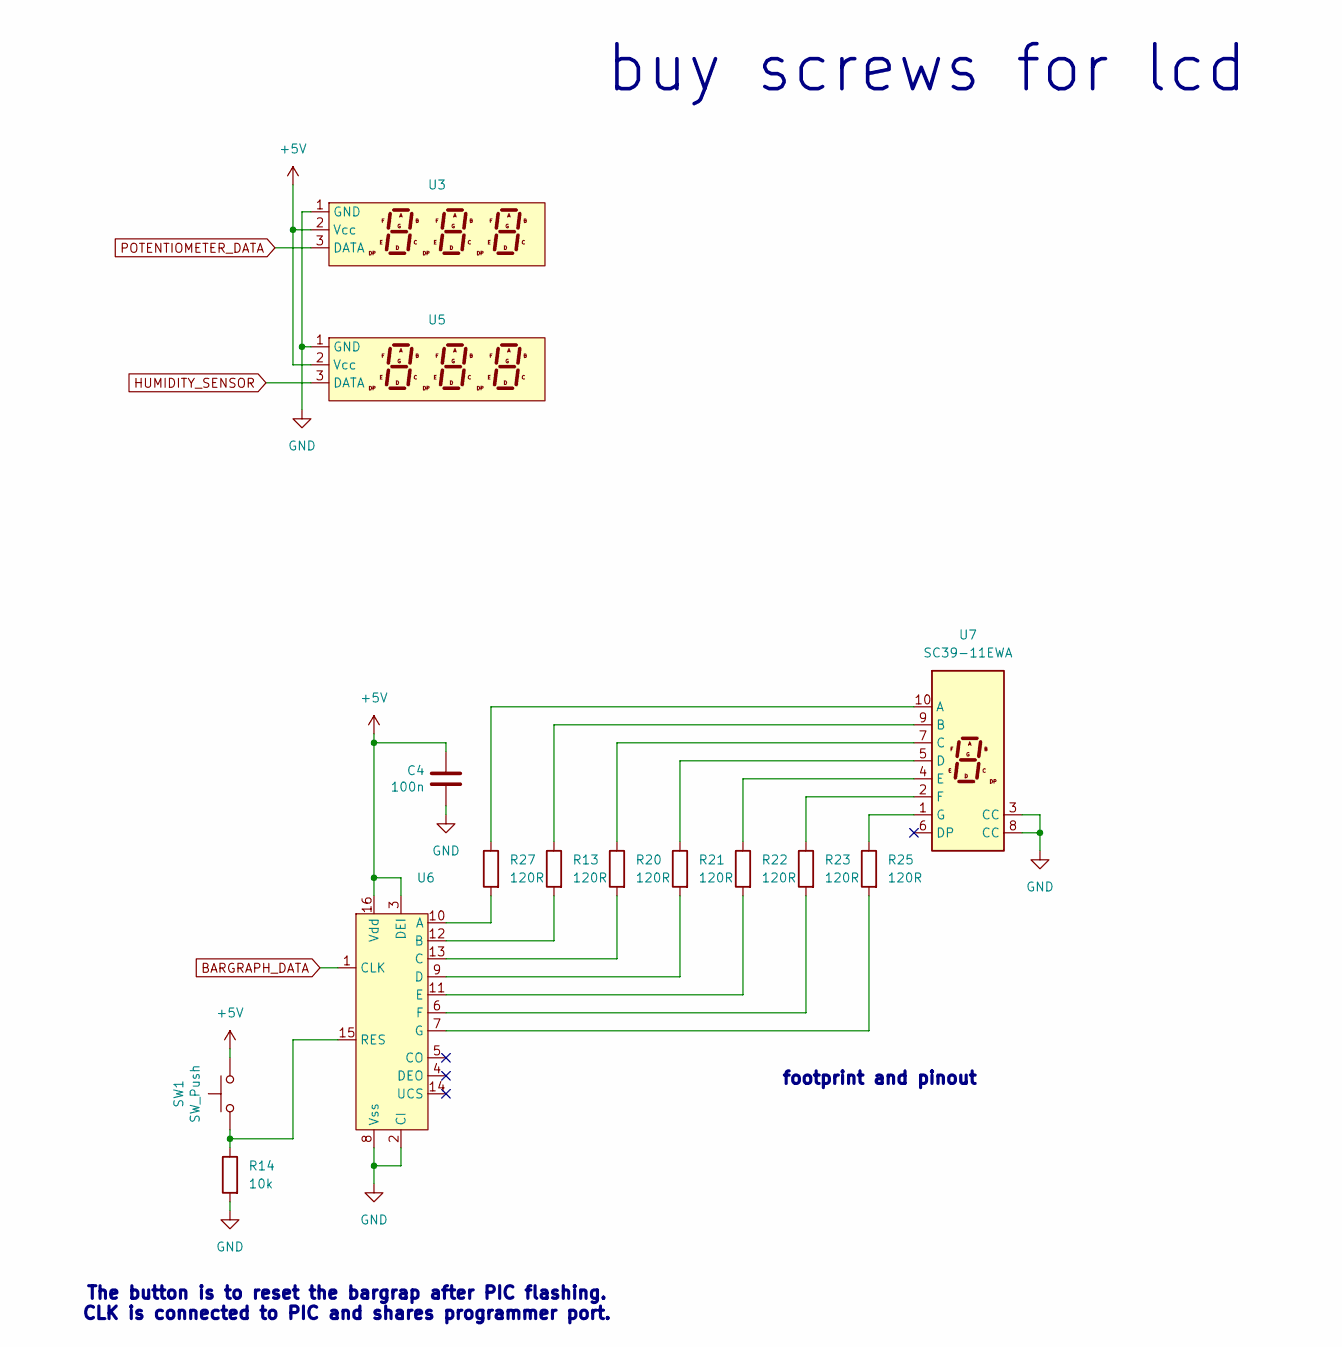
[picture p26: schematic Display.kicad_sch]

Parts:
C4: 100n; C_0603_1608Metric
R13, R20, R21, R22, R23, R25, R27: 120R; R_0603_1608Metric
R14: 10k; R_0603_1608Metric
SW1: SW_Push; SW_SPST_PTS645Sx43SMTR92
U3, U5: SegmentDisplayMounting
U6: JEITA_SOIC-16_3.9x9.9mm_P1.27mm
U7: SC39-11EWA; Sx39-1xxxxx

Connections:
+5V: C4.1, SW1.2, U3.2 (Vcc), U5.2 (Vcc), U6.3 (DEI), U6.16 (Vdd); also elsewhere on the board
BARGRAPH_DATA: U6.1 (CLK); also elsewhere on the board
GND: C4.2, R14.2, U3.1 (GND), U5.1 (GND), U6.2 (CI), U6.8 (Vss), U7.3 (CC), U7.8 (CC); also elsewhere on the board
HUMIDITY_SENSOR: U5.3 (DATA); also elsewhere on the board
unnamed: R27.2, U6.10 (A)
unnamed: R13.2, U6.12 (B)
unnamed: R20.2, U6.13 (C)
unnamed: R21.2, U6.9 (D)
unnamed: R22.2, U6.11 (E)
unnamed: R23.2, U6.6 (F)
unnamed: R25.2, U6.7 (G)
unnamed: R14.1, SW1.1, U6.15 (RES)
unnamed: R27.1, U7.10 (A)
unnamed: R13.1, U7.9 (B)
unnamed: R20.1, U7.7 (C)
unnamed: R21.1, U7.5 (D)
unnamed: R22.1, U7.4 (E)
unnamed: R23.1, U7.2 (F)
unnamed: R25.1, U7.1 (G)
POTENTIOMETER_DATA: U3.3 (DATA); also elsewhere on the board

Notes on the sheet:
footprint and pinout
buy screws for lcd
The button is to reset the bargrap after PIC flashing. CLK is connected to PIC and shares programmer port.

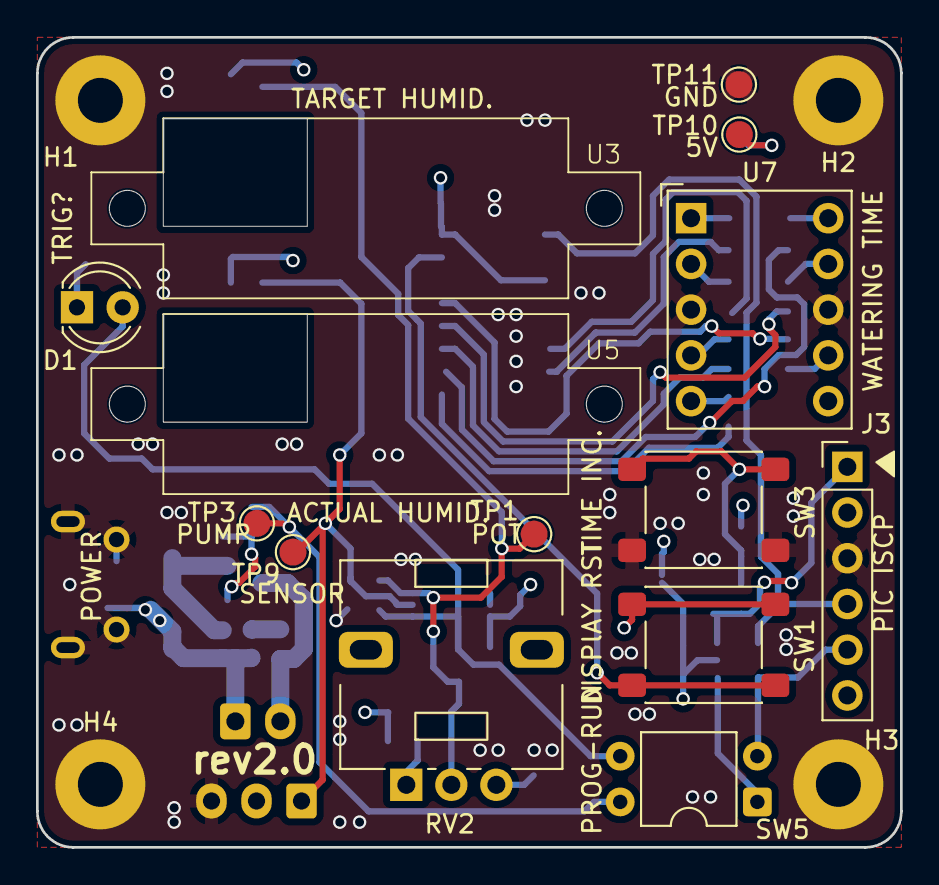
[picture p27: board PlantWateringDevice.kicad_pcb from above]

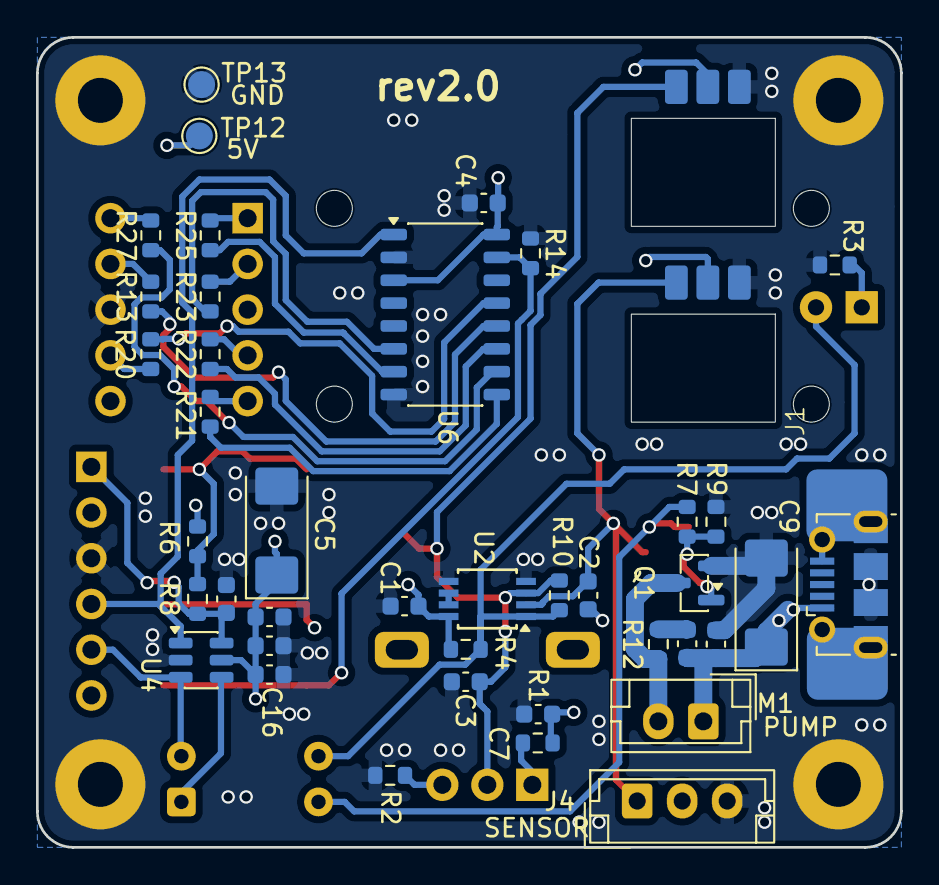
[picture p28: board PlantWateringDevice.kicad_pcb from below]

Board: 4 copper layers, 48.0 x 45.0 mm, 58 parts (40 on the bottom side), 33 nets.

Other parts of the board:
C14: 100n; C_0603_1608Metric

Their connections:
+5V: C14.1; also elsewhere on the board
unnamed 5: C14.2; also elsewhere on the board

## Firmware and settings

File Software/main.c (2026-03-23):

/**
 * @file main.c
 * @brief Plant watering controller with user-adjustable pump duration.
 *
 * @processor PIC10F202
 * @toolchain PIC-AS (MPLAB X / VS Code)
 *
 * @section hardware_config Hardware Configuration
 *
 * - GP0 (pin 1): Output - Duration feedback pulse
 *   Connected to the CD4026 clock input of a single-digit seven-segment display.
 *
 * - GP1 (pin 3): Input - Soil moisture sensor
 *   HIGH = soil is wet (no action)
 *   LOW  = soil is dry (watering required)
 *
 * - GP2 (pin 4): Output - Pump MOSFT control
 *   HIGH = pump running
 *   LOW  = pump stopped
 *
 * - GP3 (pin 2): Input - User pushbutton (active LOW, external pull-up required)
 *   Controls pump duration setting.
 *
 * @section functional_description Functional Description
 *
 * - Soil sensor is checked every hour; if dry, pump runs for the selected duration.
 * - Button press advances selected pump duration setting (1-9 levels, wrapping).
 * - The current level is visible on the seven-segment display.
 * - Each level represents 5 seconds of pump runtime (5-45 seconds total).
 * - When watering is required, GP0 outputs a pulse equal to the selected
 *   duration level.
 *
 * @section architectural_constraints Architectural Constraints
 *
 * - Hardware call stack: 2 levels (no overflow detection).
 * - Compiled stack: DISABLED to conserve code space.
 * - Assembly output MUST be inspected after each build to verify that
 *   no unintended CALL instructions are generated.
 * - Button debouncing is done on hardware side.
 * - User is not pressing the button at startup.
 * - Pump runtime is shorter than the soil-check interval; therefore,
 *   the pump cannot be activated while already running.
 * - After reprogramming, a device reset is required to synchronize
 *   the display state with the internal duration level.
 * - After power-up, the first soil moisture check is delayed by 10 seconds
 *   to allow system stabilization.
 *
 * @section timing_assumptions Timing Assumptions
 *
 * - Internal oscillator: nominal 4 MHz (uncalibrated internal RC oscillator).
 * - Instruction cycle: 1 us (Fosc/4).
 * - Base tick period: 20 ms (50 ticks = 1 second).
 * - Timing accuracy depends on internal oscillator tolerance as specified
 *   in the device datasheet (temperature and voltage dependent).
 */

/* ================================================================
 * CLOCK CONFIGURATION
 * ================================================================ */

#include "hal.h"
#include "logger.h"
#include "gpio_mapping.h"

#include "watering.h"

#include <stdint.h>
#include <stdbool.h>

/**** PIC CONFIG WORD ****/
#if !defined(TARGET_HOST) && !defined(__FRAMAC__)
#pragma config WDTE = OFF
#pragma config CP = OFF
#pragma config MCLRE = OFF
#pragma config OSC = IntRC
#endif

/**
 * @note Button and display handling depend directly on the 20 ms tick period.
 *       This could be decoupled, but doing so would require additional code
 *       that is not necessary. A 20 ms interval is acceptable for both
 *       button processing and driving the CD4026.
 */

/*@
    requires data.pump.configured_duration_level >= 1;
    requires data.pump.configured_duration_level <= 9;
    requires data.pump.remaining_cycle_levels > 0
        ==> data.pump.level_remaining_seconds > 0;
    terminates \false;
    assigns OPTION, TRISGPIO, GPIObits, data;
*/
int main(void)
{
    WATERING_LOG_INFO("PlantWatering firmware starting");

#ifdef TARGET_HOST
    static bool is_initialized = false;
    if (!is_initialized)
    {
#endif
        watering_initialize();
#ifdef TARGET_HOST
        is_initialized = true;
    }
#endif

#ifndef TARGET_HOST
    /*@
      loop invariant tick_range:
          data.time.tick < WATERING_TIME_TICKS_PER_SECOND;

      loop invariant seconds_range:
          data.time.seconds < WATERING_TIME_SECONDS_PER_MINUTE;

      loop invariant minutes_range:
          data.time.minutes < WATERING_TIME_MINUTES_PER_HOUR;

      loop invariant level_valid:
          data.pump.configured_duration_level >= 1 &&
          data.pump.configured_duration_level <= 9;

      loop invariant pump_safety:
          data.pump.remaining_cycle_levels > 0
          ==> data.pump.level_remaining_seconds > 0;

      loop invariant button_range:
          data.button_was_pressed == true ||
          data.button_was_pressed == false;

      loop invariant send_pulse_range:
          data.send_pulse_to_display == true ||
          data.send_pulse_to_display == false;

      loop invariant sending_pulse_range:
          data.sending_pulse_to_display == true ||
          data.sending_pulse_to_display == false;

      loop invariant overflow_pulse_range:
          data.display_overflow_pulse == true ||
          data.display_overflow_pulse == false;

      loop assigns data, GPIObits;
    */
    while (true)
#endif
    {
        HW_DELAY_MS(WATERING_TIME_BASE_TICK_MS);

        /* Hardware guarantee: 1-bit GPIO bitfields can only hold 0 or 1.
            WP cannot deduce this after loop havoc of the GPIObits union,
            so we state it as an assumption. This is physically guaranteed
            by the PIC10F202 hardware register design. */
        //@ admit GPIObits.GP0 == 0 || GPIObits.GP0 == 1;
        //@ admit GPIObits.GP1 == 0 || GPIObits.GP1 == 1;
        //@ admit GPIObits.GP2 == 0 || GPIObits.GP2 == 1;
        //@ admit GPIObits.GP3 == 0 || GPIObits.GP3 == 1;

        watering_handle_button();
        watering_handle_display();

        if (++data.time.tick >= WATERING_TIME_TICKS_PER_SECOND)
        {
            data.time.tick = 0;

            if (++data.time.seconds >= WATERING_TIME_SECONDS_PER_MINUTE)
            {
                data.time.seconds = 0;
                WATERING_LOG_DEBUG_LOW("Minute elapsed: %02d", data.time.minutes + 1);

                if (++data.time.minutes >= WATERING_TIME_MINUTES_PER_HOUR)
                {
                    data.time.minutes = 0;
                    WATERING_LOG_INFO("Hour elapsed - checking soil");
                    //@ admit GPIObits.GP1 == 0 || GPIObits.GP1 == 1;
                    watering_handle_sensor_check();
                }
            }

            watering_handle_pump();
        }
    }
}

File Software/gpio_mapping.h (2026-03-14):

#ifndef GPIO_MAPPING_H
#define GPIO_MAPPING_H

#include "hal.h"

/* ================================================================
 * GPIO PIN DEFINITIONS
 * ================================================================ */

#ifndef TARGET_HOST
/* Real hardware - direct register bit references */
#define GPIO_DISPLAY_DATA_OUTPUT GPIObits.GP0
#define GPIO_SOIL_SENSOR_INPUT GPIObits.GP1
#define GPIO_PUMP_MOSFET_OUTPUT GPIObits.GP2
#define GPIO_USER_BUTTON_INPUT GPIObits.GP3
#else
/* Simulation - pin numbers for JavaScript interop */
#define GPIO_DISPLAY_DATA_OUTPUT 0U
#define GPIO_SOIL_SENSOR_INPUT 1U
#define GPIO_PUMP_MOSFET_OUTPUT 2U
#define GPIO_USER_BUTTON_INPUT 3U
#endif

#endif /* GPIO_MAPPING_H */

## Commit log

2025-08-10 initial version
    [DataHandling.kicad_sch, HumiditySensor.kicad_sch, InMUX.kicad_sch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]
2025-09-07 circuit simplification
    [DataHandling.kicad_sch, Display.kicad_sch, HumiditySensor.kicad_sch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]
2025-09-07 model of 3d printed holder
    [BottomHolder.FCStd, ConnectorCutout.scad, Constants.scad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]
2025-09-25 improvements after eric's comments
    [DataHandling.kicad_sch, Display.kicad_sch, HumiditySensor.kicad_sch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]
2025-12-31 fixes before sending pcb and 3d model to production
    [DataHandling.kicad_sch, Display.kicad_sch, Mechanic.kicad_sch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]
2026-01-27 README.md cleanup
    [DataHandling.kicad_sch, Main.scad]
2026-01-27 firmware implementation
    [DataHandling.kicad_sch, Display.kicad_sch, HumiditySensor.kicad_sch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]
2026-01-30 fix #29, fix #31
    [DataHandling.kicad_sch, Display.kicad_sch, HumiditySensor.kicad_sch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]
2026-01-30 add better device photos
2026-02-22 fix #16, fix #17, fix #18, fix #19, fix #20, fix #26, fix #27, fix #28, fix #30, fix #32, fix#33, fix #34, fix #35, fix #38
    [ConnectorCutout.scad, Constants.scad, DataHandling.kicad_sch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]
2026-03-01 firmware implementation in c, draft of unit tests
    [PowerManagement.kicad_sch]
2026-03-08 fix display bug, speed up simulation
    [hal.c, main.c, watering.c]
2026-03-14 fix #57, fix #55, fix #49
    [hal.c, hal.h, main.c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]
2026-03-23 fix #64, fix #65, fix #66
    [hal.c, hal.h, main.c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]
2026-03-23 hierarchical block diagram structure in kicad
    [DataHandling.kicad_sch, Display.kicad_sch, HumiditySensor.kicad_sch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]
